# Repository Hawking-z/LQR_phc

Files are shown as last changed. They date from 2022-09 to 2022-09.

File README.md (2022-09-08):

# 基于LQR算法的平衡车

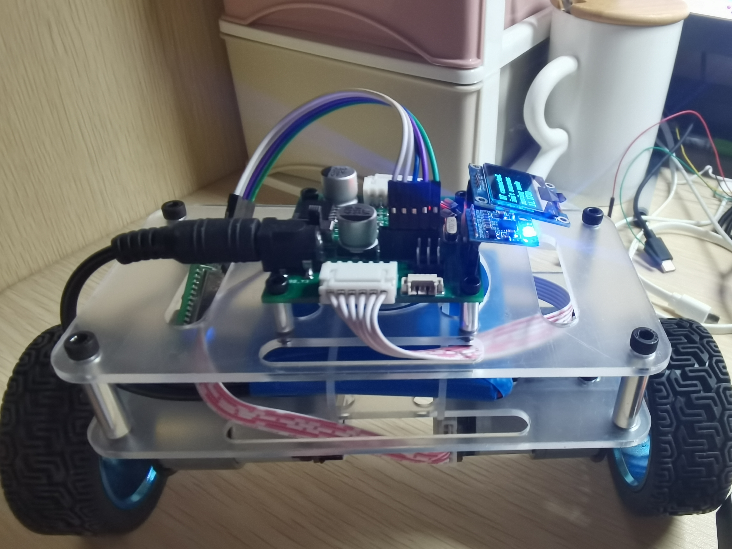
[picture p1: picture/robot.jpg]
小车


- [基于LQR算法的平衡车](#基于lqr算法的平衡车)
  - [概述](#概述)
  - [开源文件解析](#开源文件解析)
  - [硬件部分](#硬件部分)
  - [控制部分](#控制部分)
  - [机械部分](#机械部分)
  - [总结](#总结)
## 概述

  本开源项目主要分享的是一款有STM32F103C8T6控制芯片控制的平衡小车，平衡算法主要使用一阶线性倒立摆模型，在Matlab利用LQR算法计算出反馈矩阵，通过MPU6050以及电机编码器反馈实现平衡以及转向的控制。本项目主要是记录我绘制的第一块pcb以及第一次使用Markdown。

## 开源文件解析

* 建模：主要是solidworks文件，比较简单，主是为了固定电路板和电机
* 平衡车驱动板：AD文件，个人绘画的第一块板子
* matlab_source: Matlab计算文件
* MyPHC_F103C8T6: 代码

## 硬件部分

1. 主控板
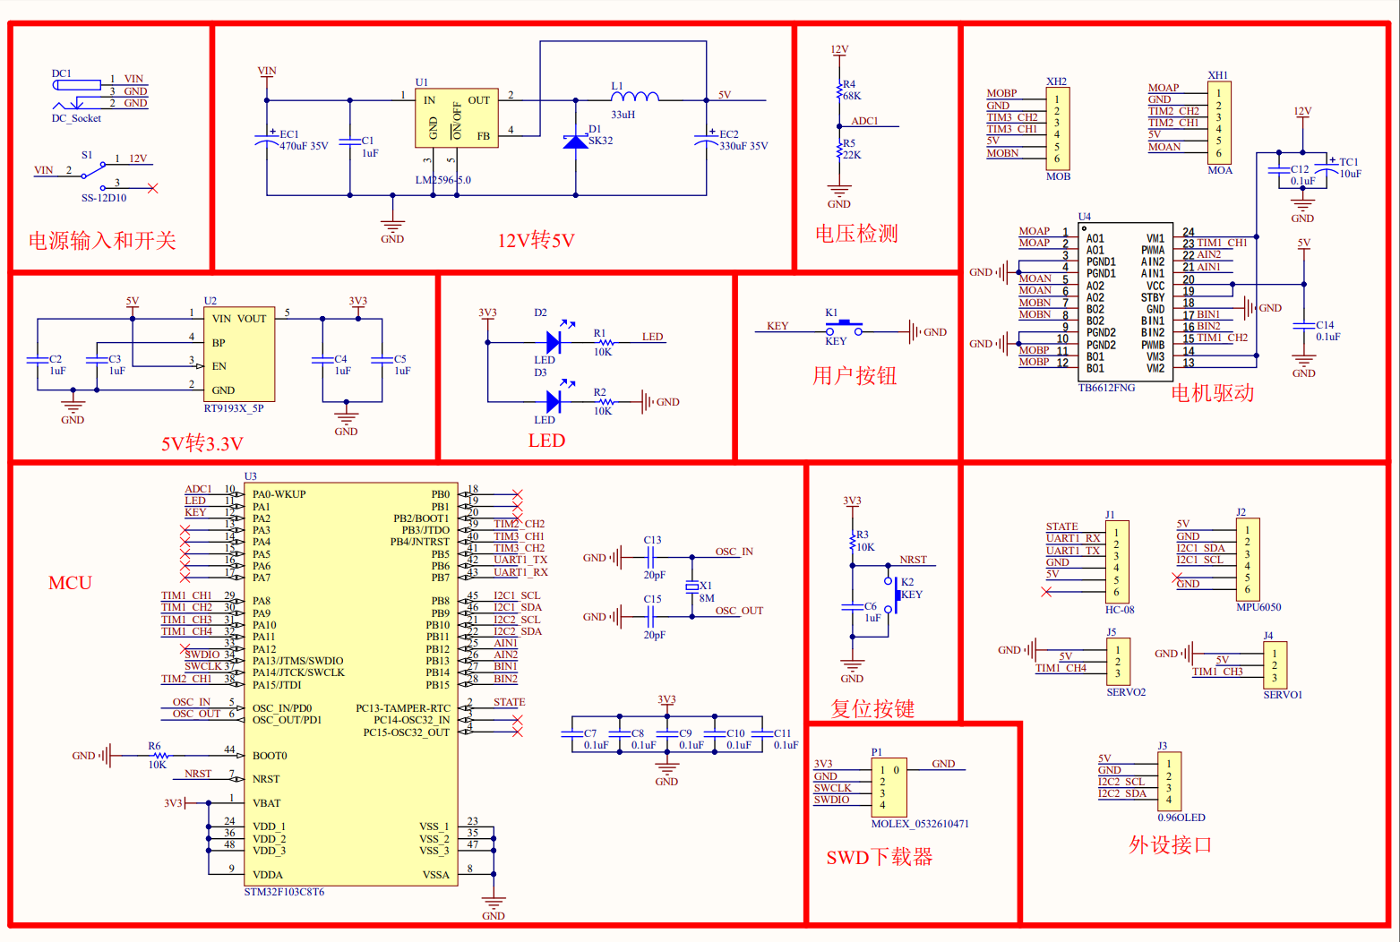
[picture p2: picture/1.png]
主控板原理图
    
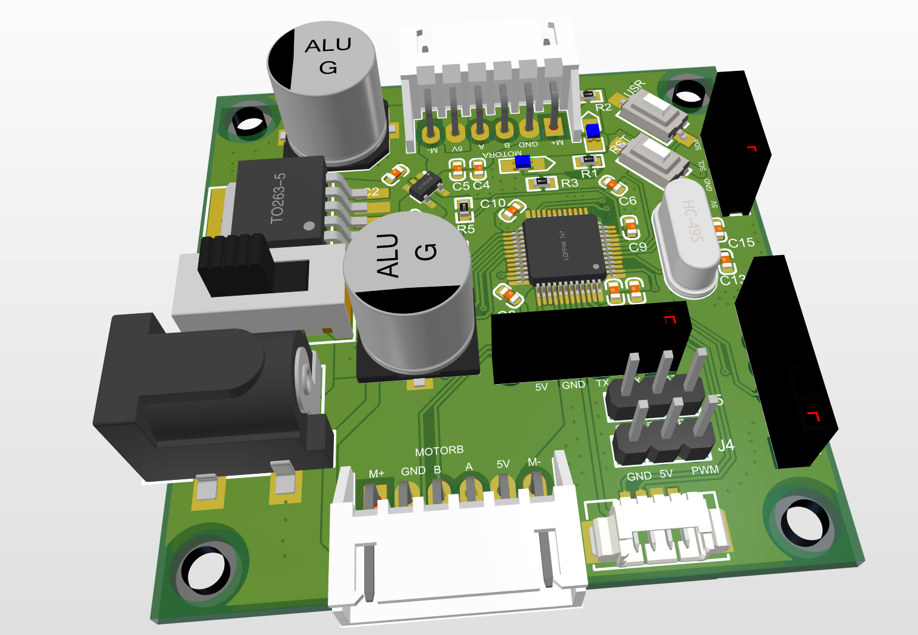
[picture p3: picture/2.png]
主控板pcb图
    
    主控板主要是集成电压转换模块，电机驱动模块，主控芯片以及一些外设接口，内容比较简单。但由于是本人第一次绘制PCB，经历了电路设计，电路绘制，元件采购再到最后的焊接，学到非常多的东西，所以这一块板子是非常具有**纪念价值**。板子中的所有功能都可正常使用，唯一不足是蓝牙接口的TX和RX没有与购买的蓝牙设备相对应，所以只能用杜邦线将RX和TX对接一下。

2. 电机
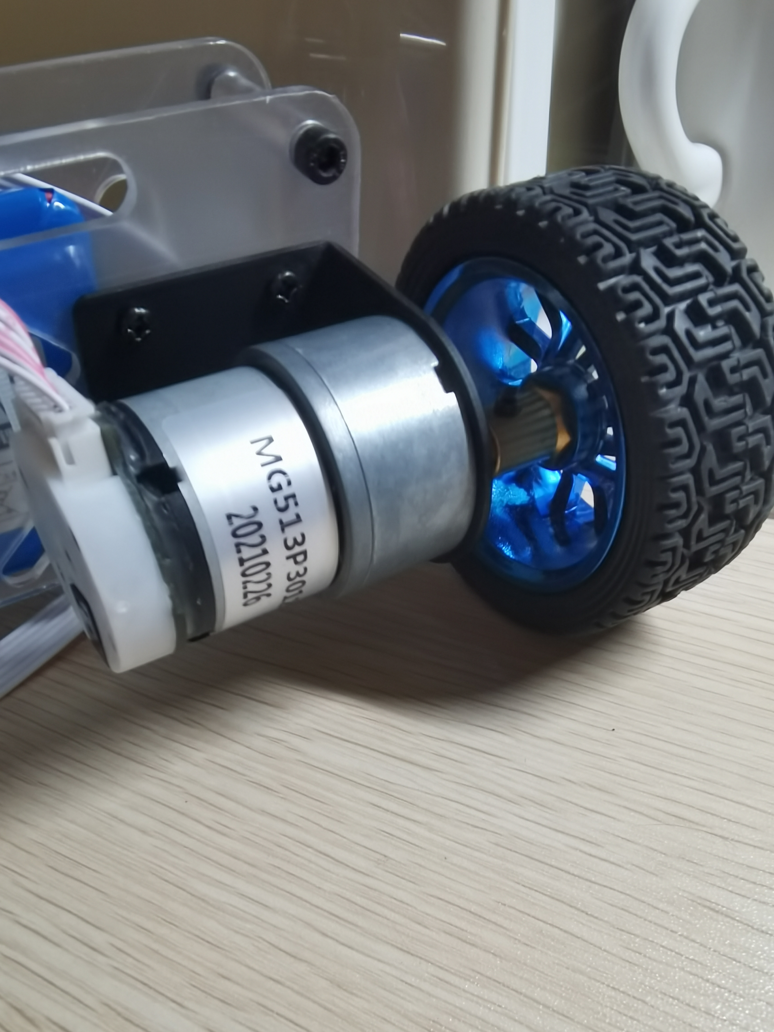
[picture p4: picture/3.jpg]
电机
    
    电机我使用的是光电编码器的直流减速电机MG513P3012V，使用这款电机主要是大一立项剩下的，拿出来使用总好过放盒子积灰。但我**不推荐**使用这种电机作为平衡车的驱动轮，最主要的原因是电机的**虚位**很大，所以很难在平衡位置实现平衡，只会在在附近来回摆动。

3. 外设
    蓝牙：HC-08

    陀螺仪: MPU6050(正点原子)

    电池: 12V2800mAh锂电池(容量无所谓，跟你设计的小车大小有关)

    屏幕: 0.96寸OLED

## 控制部分

* 物理建模

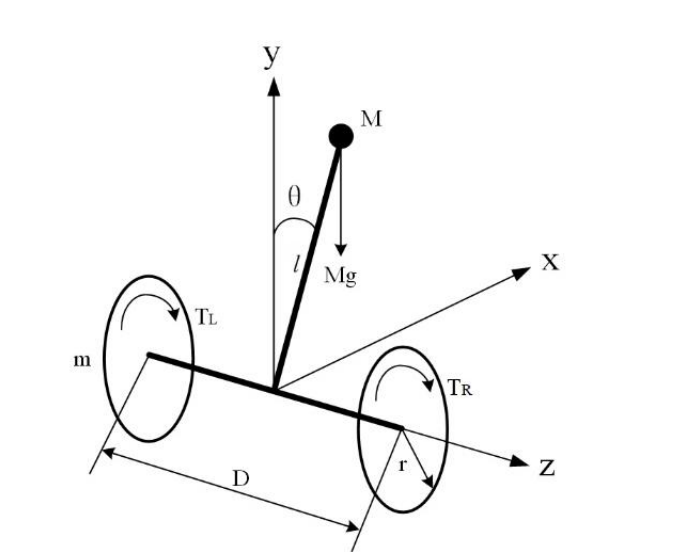
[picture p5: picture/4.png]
物理建模


---经过计算化简以及线性化处理之后就可以得到状态空间方程

方程

调整Q和R矩阵，经过matlab的lqr()函数计算，最终得到状态反馈矩阵

---

* 蓝牙控制
  
小车控制主要是使用手机蓝牙通信
在这里我使用的是蓝牙调试器，自己设计控制组件

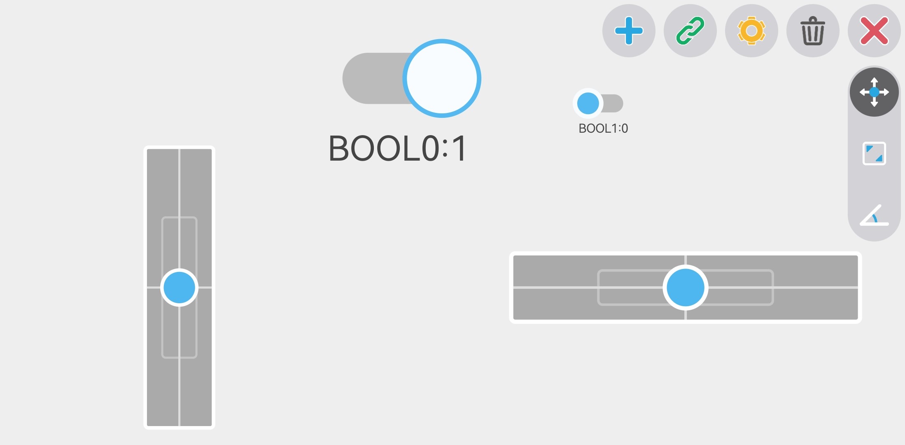
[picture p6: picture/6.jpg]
控制


## 机械部分

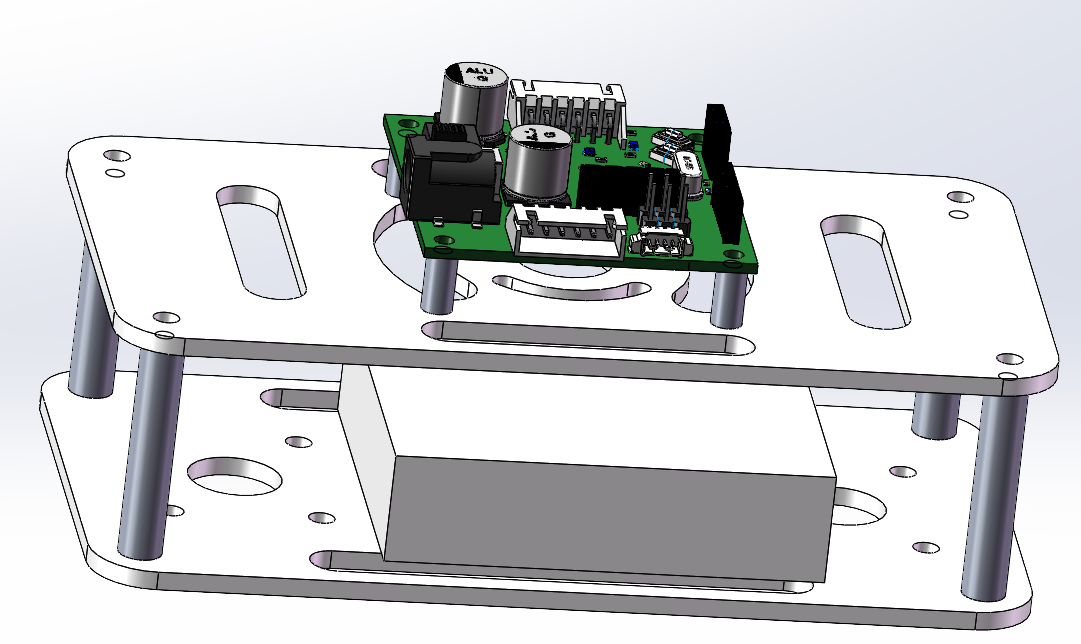
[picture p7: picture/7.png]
机械

能够固定板子和电机就行，本身结构就非常简单

## 总结

由于LQR的强鲁棒性，小车不需要过多调整参数便可实现很好的控制。

小车在静止平衡状态下由于电机虚位，会小幅度摆动，在运动状态下能够很好地根据命令运行。

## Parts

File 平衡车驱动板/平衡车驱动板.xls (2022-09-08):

Comment | Description | Designator | Footprint | LibRef | Quantity
1uF | 无极性电容 | C1, C2, C3, C4, C5, C6 | 0603C | CAP | 6
0.1uF | 无极性电容 | C7, C8, C9, C10, C11, C12, C14 | 0603C | CAP | 7
20pF | 无极性电容 | C13, C15 | 0603C | CAP | 2
SK32 | 肖特基二极管 | D1 | SOD-123 | DIODE SCHOTTKY | 1
LED |  | D2, D3 | LED-0805B | LED | 2
DC_Socket |  | DC1 | DC-050 | DC_Socket | 1
470uF 35V | 贴片电解电容 | EC1 | SMD-EC10X10X10 | SMD_ECAP | 1
330uF 35V | 贴片电解电容 | EC2 | SMD-EC10X10X10 | SMD_ECAP | 1
HC-08 |  | J1 | Fe-HDR1X6/2.54-S | Female HDR1X6 | 1
MPU6050 |  | J2 | Fe-HDR1X6/2.54-S | Female HDR1X6 | 1
0.96OLED |  | J3 | Fe-HDR1X4/2.54-S | Female HDR1X4 | 1
SERVO1 |  | J4 | Pin HDR1X3/2.54mm-S | Pin HDR1X3 | 1
SERVO2 |  | J5 | Pin HDR1X3/2.54mm-S | Pin HDR1X3 | 1
KEY |  | K1, K2 | SMD-3X6X2.5 | KEY | 2
33uH | INDUCTOR | L1 | 0630L | INDUCTOR | 1
MOLEX_0532610471 | MOLEX_0532610471,4Pin,1.25mm | P1 | MOLEX 0532610471 | MOLEX_0532610471 | 1
10K |  | R1, R2, R3, R6 | 0603R | RES | 4
68K |  | R4 | 0603R | RES | 1
22K |  | R5 | 0603R | RES | 1
SS-12D10 |  | S1 | SS-12D10 | SS-12D10 | 1
10uF | 钽电容 | TC1 | TAJ-B/3528 | TCAP | 1
LM2596-5.0 | DC降压芯片 | U1 | TO263-5A | LM2596-5.0 | 1
RT9193X_5P | 5V转3.3V | U2 | SOT23-5L | RT9193X_5P | 1
STM32F103C8T6 |  | U3 | LQFP48 7X7 | STM32F103C8T6 | 1
TB6612FNG | 双电机驱动 | U4 | TB6612-SSOP-24 | TB6612FNG | 1
8M | 2脚无源脚晶振 | X1 | OSC HC-49S | XTAL-2P | 1
MOA |  | XH1 | XH6/2.54mm/90 | XH6 | 1
MOB |  | XH2 | XH6/2.54mm/90 | XH6 | 1

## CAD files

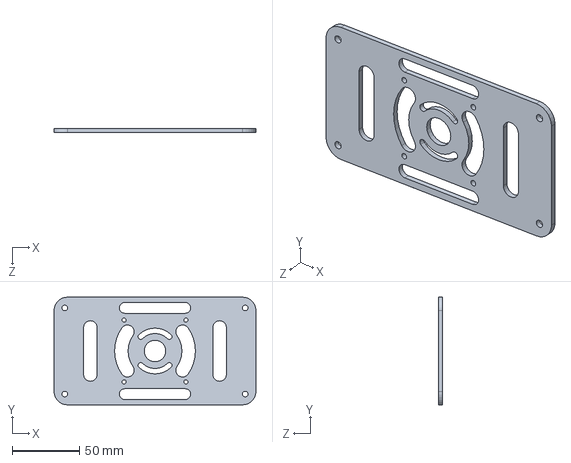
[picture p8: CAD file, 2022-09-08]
建模/上层板.SLDPRT
150.0 x 80.0 x 3.00 mm

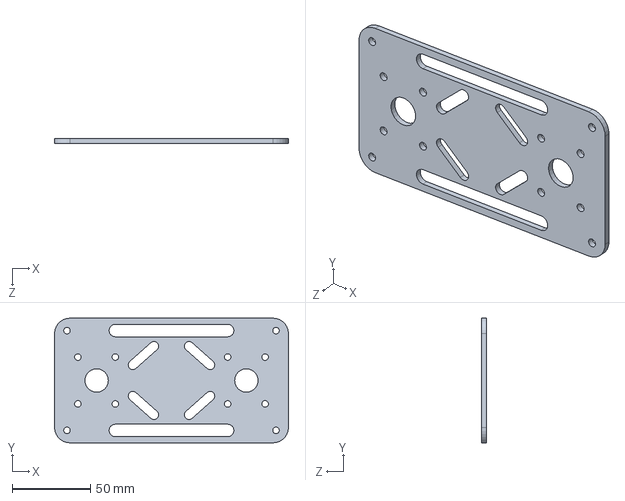
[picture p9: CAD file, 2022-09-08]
建模/下层板.SLDPRT
150.0 x 80.0 x 3.00 mm

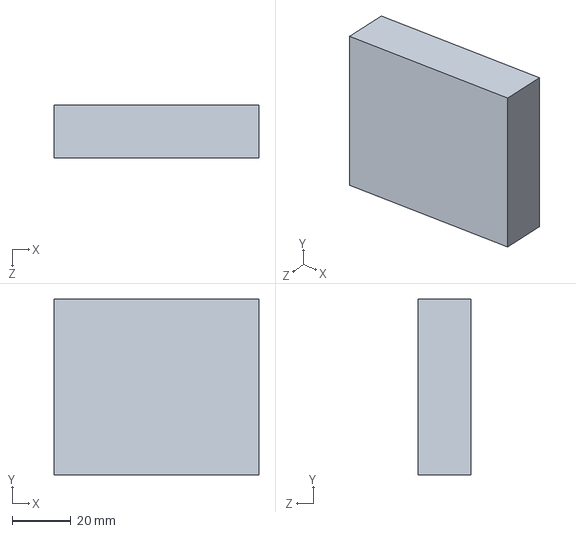
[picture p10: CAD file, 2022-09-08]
建模/电池.SLDPRT
70.0 x 60.0 x 18.0 mm

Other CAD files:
建模/上层板.DXF
建模/下层板.DXF

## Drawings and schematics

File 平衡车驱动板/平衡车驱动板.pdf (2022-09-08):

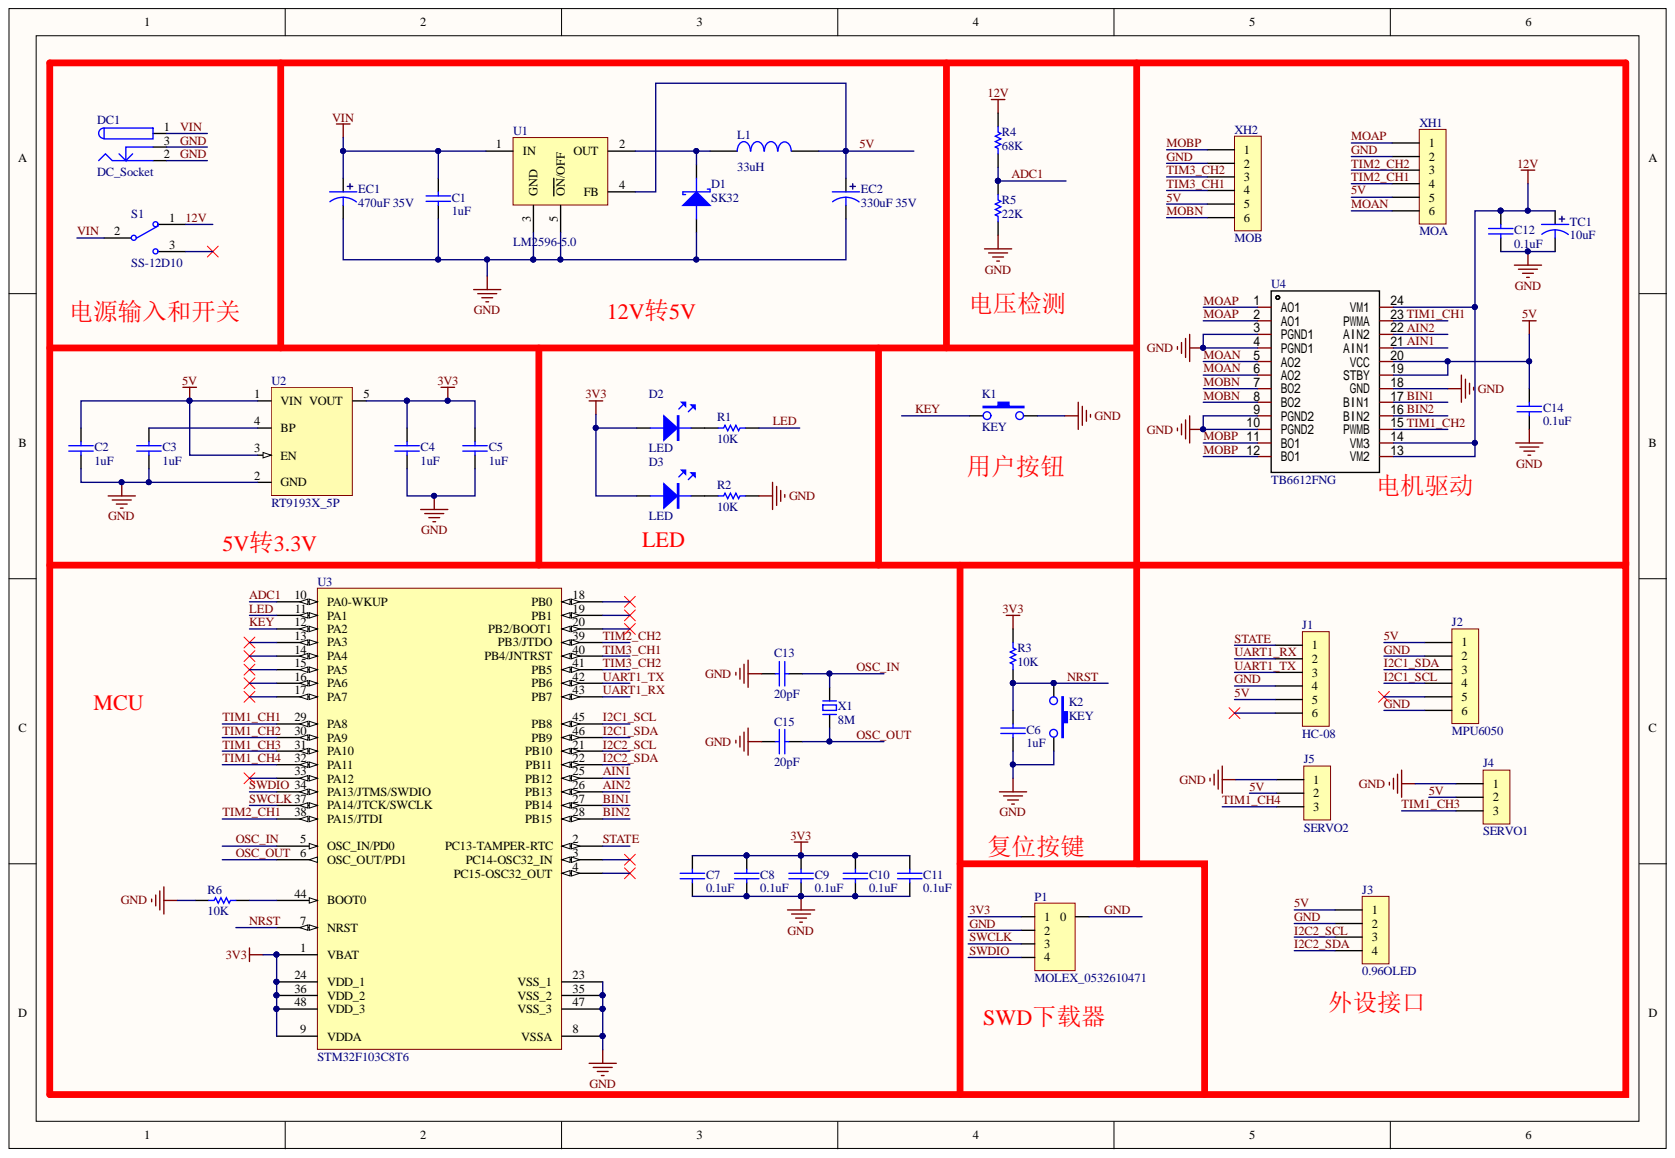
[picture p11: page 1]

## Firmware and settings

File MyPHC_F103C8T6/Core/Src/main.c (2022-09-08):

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
/* Includes ------------------------------------------------------------------*/
#include "main.h"
#include "cmsis_os.h"
#include "adc.h"
#include "crc.h"
#include "dma.h"
#include "i2c.h"
#include "tim.h"
#include "usart.h"
#include "gpio.h"

/* USER CODE BEGIN Includes */
#include "robot.h"
/* USER CODE END Includes */


void SystemClock_Config(void);
void MX_FREERTOS_Init(void);
/**
  * @brief  The application entry point.
  * @retval int
  */
int main(void)
{
  /* MCU Configuration--------------------------------------------------------*/

  /* Reset of all peripherals, Initializes the Flash interface and the Systick. */
  HAL_Init();

  /* Configure the system clock */
  SystemClock_Config();

  /* Initialize all configured peripherals */
  MX_GPIO_Init();
  MX_CRC_Init();
  MX_I2C1_Init();
  MX_TIM1_Init();
  MX_TIM2_Init();
  MX_TIM3_Init();
  MX_USART1_UART_Init();
  MX_DMA_Init();
  MX_I2C2_Init();
  MX_ADC1_Init();
  /* USER CODE BEGIN 2 */
  HAL_TIM_Encoder_Start(&htim2,TIM_CHANNEL_1);
  HAL_TIM_Encoder_Start(&htim2,TIM_CHANNEL_2);
  HAL_TIM_Encoder_Start(&htim3,TIM_CHANNEL_1);
  HAL_TIM_Encoder_Start(&htim3,TIM_CHANNEL_2);
  HAL_TIM_Base_Start_IT(&htim2);
  HAL_TIM_Base_Start_IT(&htim3);
  HAL_TIM_PWM_Start(&htim1,TIM_CHANNEL_1);
  HAL_TIM_PWM_Start(&htim1,TIM_CHANNEL_2);
  // HAL_TIM_PWM_Start(&htim1,TIM_CHANNEL_3);
  // HAL_TIM_PWM_Start(&htim1,TIM_CHANNEL_4);
  robot_init();
  /* USER CODE END 2 */

  /* Init scheduler */
  osKernelInitialize();  /* Call init function for freertos objects (in freertos.c) */
  MX_FREERTOS_Init();

  /* Start scheduler */
  osKernelStart();

  /* We should never get here as control is now taken by the scheduler */
  /* Infinite loop */
  /* USER CODE BEGIN WHILE */
  while (1)
  {
    /* USER CODE END WHILE */

    /* USER CODE BEGIN 3 */
  }
  /* USER CODE END 3 */
}

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
/**
  * @brief  Period elapsed callback in non blocking mode
  * @note   This function is called  when TIM4 interrupt took place, inside
  * HAL_TIM_IRQHandler(). It makes a direct call to HAL_IncTick() to increment
  * a global variable "uwTick" used as application time base.
  * @param  htim : TIM handle
  * @retval None
  */
void HAL_TIM_PeriodElapsedCallback(TIM_HandleTypeDef *htim)
{
  /* USER CODE BEGIN Callback 0 */
  if(htim->Instance == TIM2)
  {
    Robot_Encoder(1);
  }
  else if (htim->Instance == TIM3)
  {
    Robot_Encoder(0);
  }
  

  /* USER CODE END Callback 0 */
  if (htim->Instance == TIM4) {
    HAL_IncTick();
  }
}

/**
  * @brief  This function is executed in case of error occurrence.
  * @retval None
  */
void Error_Handler(void)
{
  /* USER CODE BEGIN Error_Handler_Debug */
  /* User can add his own implementation to report the HAL error return state */
  __disable_irq();
  while (1)
  {
  }
  /* USER CODE END Error_Handler_Debug */
}

#ifdef  USE_FULL_ASSERT
/**
  * @brief  Reports the name of the source file and the source line number
  *         where the assert_param error has occurred.
  * @param  file: pointer to the source file name
  * @param  line: assert_param error line source number
  * @retval None
  */
void assert_failed(uint8_t *file, uint32_t line)
{
  /* USER CODE BEGIN 6 */
  /* User can add his own implementation to report the file name and line number,
     ex: printf("Wrong parameters value: file %s on line %d\r\n", file, line) */
  /* USER CODE END 6 */
}
#endif /* USE_FULL_ASSERT */

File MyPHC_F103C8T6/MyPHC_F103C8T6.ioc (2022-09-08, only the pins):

Mcu.UserName=STM32F103C8Tx
PA0-WKUP.Signal=ADCx_IN0
PA1.Signal=GPIO_Output
PA10.Signal=S_TIM1_CH3
PA11.Signal=S_TIM1_CH4
PA12.Signal=GPIO_Output
PA13.Signal=SYS_JTMS-SWDIO
PA14.Signal=SYS_JTCK-SWCLK
PA15.Signal=S_TIM2_CH1_ETR
PA2.Signal=GPXTI2
PA8.Signal=S_TIM1_CH1
PA9.Signal=S_TIM1_CH2
PB10.Signal=I2C2_SCL
PB11.Signal=I2C2_SDA
PB12.Signal=GPIO_Output
PB13.Signal=GPIO_Output
PB14.Signal=GPIO_Output
PB15.Signal=GPIO_Output
PB3.Signal=S_TIM2_CH2
PB4.Signal=S_TIM3_CH1
PB5.Signal=S_TIM3_CH2
PB6.Signal=USART1_TX
PB7.Signal=USART1_RX
PB8.Signal=I2C1_SCL
PB9.Signal=I2C1_SDA
PC13-TAMPER-RTC.Signal=GPXTI13
PD0-OSC_IN.Signal=RCC_OSC_IN
PD1-OSC_OUT.Signal=RCC_OSC_OUT

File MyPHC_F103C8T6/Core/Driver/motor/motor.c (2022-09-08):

#include "motor.h"
#include "math.h"
#define PPR 500
#define REDUCTION_RATIO 30
#define SOFT_RATIO 4

#define RPM2RADS 0.10471975

void motor_init(motor*obj, PID_config pid_config,hardware_config hw_config)
{
    obj->fdb_v = 0;
    obj->fdb_rpm = 0;
    obj->code.round = 0;
    obj->code.encoder_cnt = 0;
    obj->stop = 1;
    obj->pid.config = pid_config;
    obj->hw_config = hw_config;
}

void motor_pwm_setccr(motor * obj,uint16_t ccr)
{
    __HAL_TIM_SET_COMPARE(obj->hw_config.pwm_htim_handle,obj->hw_config.pwm_channel,ccr);
}

void motor_stop(motor * obj)
{
    motor_pwm_setccr(obj,0);
    obj->ref_v = 0;
    obj->ref_rpm = 0;
    HAL_GPIO_WritePin(obj->hw_config.GPIO,obj->hw_config.PIN1,GPIO_PIN_RESET);
    HAL_GPIO_WritePin(obj->hw_config.GPIO,obj->hw_config.PIN2,GPIO_PIN_RESET);
}

void motor_control(motor * obj, float output)
{
    if(obj->stop)
    {
        motor_stop(obj);
        return;
    }
    if(output > 0)
    {
        HAL_GPIO_WritePin(obj->hw_config.GPIO,obj->hw_config.PIN1,GPIO_PIN_RESET);
        HAL_GPIO_WritePin(obj->hw_config.GPIO,obj->hw_config.PIN2,GPIO_PIN_SET);
    }
    else
    {
        HAL_GPIO_WritePin(obj->hw_config.GPIO,obj->hw_config.PIN1,GPIO_PIN_SET);
        HAL_GPIO_WritePin(obj->hw_config.GPIO,obj->hw_config.PIN2,GPIO_PIN_RESET);
    }
    motor_pwm_setccr(obj,fabsf(output));
}

void motor_calc(motor * obj)
{
    if(obj->stop)
    {
        motor_stop(obj);
        return;
    }
    //计算
    obj->pid.fdb = obj->fdb_v;
    obj->pid.ref = obj->ref_v;
    PID_Calc(&obj->pid);
    
    motor_control(obj,obj->pid.output);
}


void motor_getvelocity(motor * obj)
{
    obj->code.last_encoder_cnt = obj->code.encoder_cnt;
    obj->code.encoder_cnt = __HAL_TIM_GET_COUNTER(obj->hw_config.encoder_htim_handle) + obj->code.round * 65536;
    obj->fdb_rpm = 0.95*((float)(obj->code.encoder_cnt-obj->code.last_encoder_cnt))*(1000.0f/TIME)*60.0f/(SOFT_RATIO*PPR*REDUCTION_RATIO) + 0.05*obj->fdb_rpm;
    obj->fdb_v = obj->fdb_rpm *RPM2RADS;
}

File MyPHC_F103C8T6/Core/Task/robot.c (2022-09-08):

#include "robot.h"
#define CHASSIS_RADIUS 0.0325

robot PHC;

void robot_init()
{
    BSP_I2C_Init();
    BSP_UART_Init();
    CRC16_Init();
    HAL_ADC_Start_DMA(&hadc1, (uint32_t *)&PHC.adc_data, 1);
    //延时200毫秒
    HAL_Delay(200);
    //进行初始化
    // Olde初始化
    Oled_Init(&PHC.oled);
    HAL_Delay(200);
    //陀螺仪初始化
    MPU6050_config imu_config;
    imu_config.addr = 0x68;
    imu_config.bsp_i2c_index = 0;
    imu_config.accelbias[0] = 0;
    imu_config.accelbias[1] = 0;
    imu_config.accelbias[2] = 0;
    MPU6050_Create(&PHC.imu, &imu_config);
    //蓝牙初始化
    bt_config BTconfig;
    BTconfig.bsp_uart_index = 0;
    BTconfig.rx_len = 20;
    BlueTooth_Init(&PHC.bluetooth, &BTconfig);
    //电机初始化
    PID_config pid_motor_left_config;
    PID_config pid_motor_right_config;
    PID_SetConfig(&pid_motor_left_config, 5000, 1000, 3000, 1000, 65535);
    PID_SetConfig(&pid_motor_right_config, 5000, 1000, 3000, 1000, 65535);
    hardware_config hw_left_motor_config;
    hardware_config hw_right_motor_config;
    hw_left_motor_config.GPIO = GPIOB;
    hw_left_motor_config.PIN1 = GPIO_PIN_12;
    hw_left_motor_config.PIN2 = GPIO_PIN_13;
    hw_left_motor_config.encoder_htim_handle = &htim2;
    hw_left_motor_config.pwm_htim_handle = &htim1;
    hw_left_motor_config.pwm_channel = TIM_CHANNEL_1;
    hw_right_motor_config.GPIO = GPIOB;
    hw_right_motor_config.PIN1 = GPIO_PIN_14;
    hw_right_motor_config.PIN2 = GPIO_PIN_15;
    hw_right_motor_config.encoder_htim_handle = &htim3;
    hw_right_motor_config.pwm_htim_handle = &htim1;
    hw_right_motor_config.pwm_channel = TIM_CHANNEL_2;
    motor_init(&PHC.motor_left, pid_motor_left_config, hw_left_motor_config);
    motor_init(&PHC.motor_right, pid_motor_right_config, hw_right_motor_config);

    float matrix[12] = 
    {
        -66.0087,-110.0825 ,-232.8395  ,-41.4499  , 56.6947 ,  26.7274,
        -66.0087,-110.0825 ,-232.8395  ,-41.4499  ,-56.6947 , -26.7274,
    };
    lqr_set_matrix_K(&PHC.lqr,matrix);
    PHC.lqr.Outputmax = 100;             
}

void StateCalc(robot * obj)
{
    obj->speed = (-obj->motor_left.fdb_v + obj->motor_right.fdb_v)/2*CHASSIS_RADIUS;
    obj->displacement +=obj->speed*TIME/1000;
    if(obj->bluetooth.rxdata.cd.ch1!=0)
    {
        obj->displacement = 0;
    }
}


void Robot_Command()
{
    PHC.last_mode = PHC.mode;
    PHC.mode = PHC.bluetooth.rxdata.cd.stop & PHC.bluetooth.isConnect & PHC.imu.bias_init_success;
    if (PHC.mode != PHC.last_mode)
        PHC.oled.update2 = 1;
    PHC.motor_left.stop = !PHC.mode;
    PHC.motor_right.stop = !PHC.mode;
    if(PHC.bluetooth.rxdata.cd.reset)
    {
        bsp_soft_rest();
    }
    if(PHC.mode)
    {
        StateCalc(&PHC);
        PHC.lqr.StateFeedBack[0] = PHC.displacement;
        PHC.lqr.StateFeedBack[1] = PHC.speed;
        PHC.lqr.StateFeedBack[2] = -PHC.imu.data.euler[1];
        PHC.lqr.StateFeedBack[3] = -PHC.imu.data.gyro[1];
        PHC.lqr.StateFeedBack[4] = -PHC.imu.data.yaw;
        PHC.lqr.StateFeedBack[5] = -PHC.imu.data.gyro[0];
        PHC.lqr.StateRef[0] = 0;
        PHC.lqr.StateRef[1] = (float)PHC.bluetooth.rxdata.cd.ch1/200.0f;
        PHC.lqr.StateRef[2] = 0.021;
        PHC.lqr.StateRef[3] = 0;
        PHC.lqr.StateRef[4] += (float)PHC.bluetooth.rxdata.cd.ch0/4000.0f;
        PHC.lqr.StateRef[5] = 0;
        lqr_calc(&PHC.lqr);
        float ccr_l,ccr_r;
        ccr_l = -PHC.lqr.Output[0] / PHC.lqr.Outputmax * 65535 ;
        ccr_r = PHC.lqr.Output[1] / PHC.lqr.Outputmax * 65535 ;
        motor_control(&PHC.motor_left,ccr_l);
        motor_control(&PHC.motor_right,ccr_r);
    }
    else{
        motor_stop(&PHC.motor_left);
        motor_stop(&PHC.motor_right);
        PHC.speed = 0;
        PHC.displacement = 0;
        PHC.lqr.StateRef[4] = -PHC.imu.data.yaw;
    }
}

void Robot_Encoder(uint8_t choice)
{
    if (choice)
    {
        if (__HAL_TIM_IS_TIM_COUNTING_DOWN(&htim2))
        {
            PHC.motor_left.code.round--;
        }
        else
        {
            PHC.motor_left.code.round++;
        }
    }
    else
    {
        if (__HAL_TIM_IS_TIM_COUNTING_DOWN(&htim3))
        {
            PHC.motor_right.code.round--;
        }
        else
        {
            PHC.motor_right.code.round++;
        }
    }
}

void default_loop()
{
    static uint8_t count1 = 0;
    count1++;
    if (count1 > 100)
    {
        count1 = 0;
        HAL_GPIO_TogglePin(GPIOA, GPIO_PIN_1);
    if (HAL_GPIO_ReadPin(GPIOC, GPIO_PIN_13))
    {
        if (PHC.bluetooth.isConnect == 0)
            PHC.oled.update4 = 1;
        PHC.bluetooth.isConnect = 1;
    }
    else
    {
        if (PHC.bluetooth.isConnect == 1)
            PHC.oled.update4 = 1;
        PHC.bluetooth.isConnect = 0;
    }
    }
    static uint8_t count2 = 0;
    count2++;
    if (count2 > 40)
    {
        count2 = 0;
        PHC.voltage = (float)PHC.adc_data / 4096 * 3.3 * 90 / 22;
        PHC.oled.update1 = 1;
    }
    
    if (!PHC.bluetooth.isConnect)
        memset(&PHC.bluetooth.rxdata.cd,0,sizeof(PHC.bluetooth.rxdata.cd));
}

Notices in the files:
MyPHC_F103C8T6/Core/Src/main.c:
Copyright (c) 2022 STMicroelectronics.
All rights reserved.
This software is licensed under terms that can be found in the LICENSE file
